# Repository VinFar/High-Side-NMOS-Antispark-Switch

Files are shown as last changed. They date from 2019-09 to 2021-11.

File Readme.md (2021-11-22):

High Side milliOhm NMOS Anti Spark Switch
===
# Introduction

This PCB is an Anti-Spark switch for high capacitive loads (100A, 60V) and was especially designed for electric longboards.
It uses 10 TPW1R306PL milliOhm N-MOSFET, which have a Rdson of around 90 uOhm in the worst case,
which theoretically enables a maximum current of around 125A with sufficient cooling.

Inspired by the [DieBieMS](https://github.com/DieBieEngineering/DieBieMS) it uses a BQ76200PWR HighSide MOSFET driver,
to enable the high switching with NMOS.

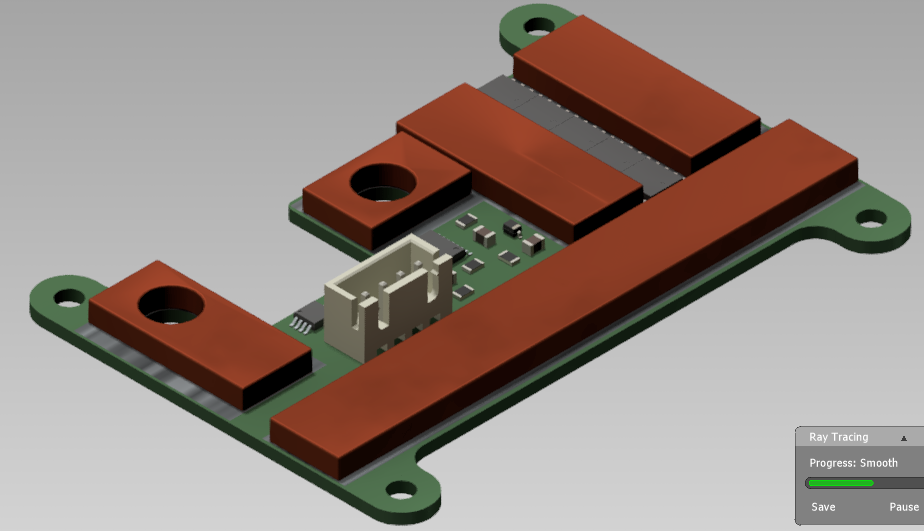
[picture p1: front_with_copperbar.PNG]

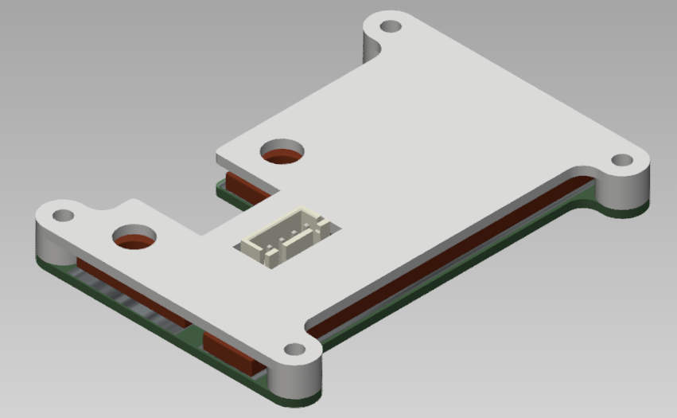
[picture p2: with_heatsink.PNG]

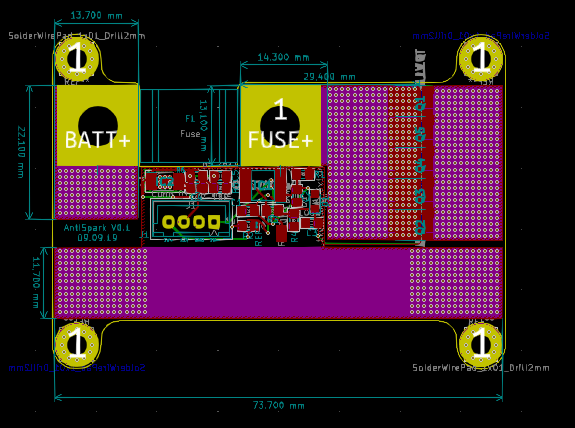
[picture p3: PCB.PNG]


## Features

The PCB includes the following features:
  - dimensions: 74mm x 38.2mm
  - maximum current of at least 125A (more with additional copper and cooling)
  - maximum voltage of 60V
  - controlled dI/dt with capacitor and current limiting resistor
  - 10 TPW1R306PL N-channel MOSFET
  - BQ76200PWR High Side MOSFET Driver
  - A TPS7A4101DGNR 12V 50mA LDO
  - A holder for a LittleFuse BF1
  - 4 pin JST XH connector for external switch or MCU
  - exposed pcb traces to add solder or a copper bar for lower resistance

### Versions
  - V0.1 is the initial version (08.09.19)
  - V0.2 uses 10 TPW1R306PL mosfet instead of two IRFS7530 (09.09.19)

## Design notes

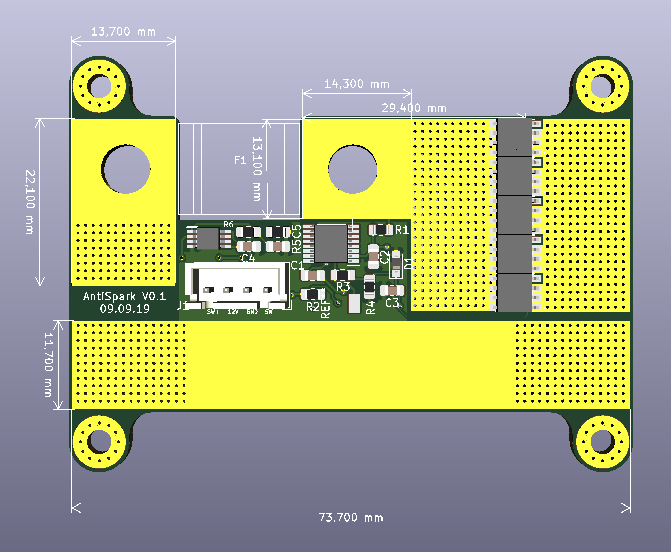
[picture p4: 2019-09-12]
front.PNG

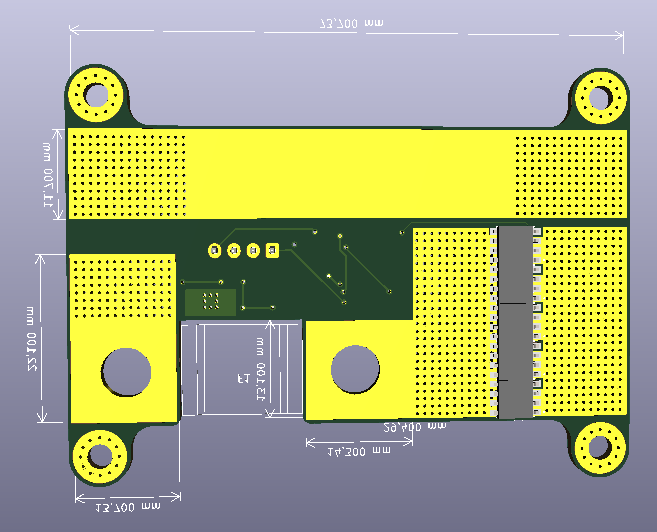
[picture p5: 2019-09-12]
back.PNG

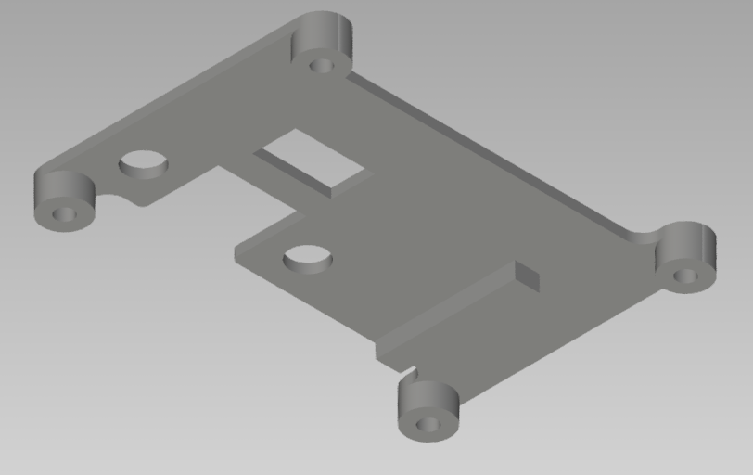
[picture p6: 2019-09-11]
heatsink.PNG

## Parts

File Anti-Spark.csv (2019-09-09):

Reference | Quantity | Value | Footprint | Datasheet | Description | Height | Manufacturer_Name | Manufacturer_Part_Number | Mouser Part Number | Mouser Price/Stock
C1 C4 C5 | 3 | 1uF | Capacitor_SMD:C_0805_2012Metric_Pad1.15x1.40mm_HandSolder | ~
C2 C3 | 2 | 100nF | Capacitor_SMD:C_0805_2012Metric_Pad1.15x1.40mm_HandSolder | ~
D1 | 1 | 18V | Diode_SMD:D_SOD-323_HandSoldering | ~
F1 | 1 | Fuse | SamacSys_Parts:littleFuseBF1 | ~
IC1 | 1 | BQ76200PWR | SOP65P640X120-16N | http://www.ti.com/lit/gpn/bq76200 | High-Side N-Channel FET Driver | 1.2 | Texas Instruments | BQ76200PWR | 595-BQ76200PWR | https://www.mouser.com/Search/Refine.aspx?Keyword=595-BQ76200PWR
IC2 | 1 | TPS7A4101DGNR | SOP65P490X110-9N | http://www.ti.com/lit/gpn/tps7a4101 | 50V Input, 50mA, Single Output Low-Dropout Linear Regulator | 1.1 | Texas Instruments | TPS7A4101DGNR | 595-TPS7A4101DGNR | https://www.mouser.com/Search/Refine.aspx?Keyword=595-TPS7A4101DGNR
J1 | 1 | Conn_01x04_Male | Connector_JST:JST_XH_B4B-XH-A_1x04_P2.50mm_Vertical | ~
Q1 Q2 | 2 | IRFS7530TRL7PP | SamacSys_Parts:IRFS7530 | https://componentsearchengine.com/Datasheets/1/IRFS7530TRL7PP.pdf | MOSFET 60V 240A StrongIRFET D2PAK-7 Infineon IRFS7530TRL7PP N-channel MOSFET Transistor, 240 A, 60 V, 7-Pin D2PAK |  | Infineon | IRFS7530TRL7PP | 942-IRFS7530TRL7PP | https://www.mouser.com/Search/Refine.aspx?Keyword=942-IRFS7530TRL7PP
R1 | 1 | 100 | Resistor_SMD:R_0805_2012Metric_Pad1.15x1.40mm_HandSolder | ~
R2 | 1 | 0 | Resistor_SMD:R_0805_2012Metric_Pad1.15x1.40mm_HandSolder | ~
R3 | 1 | 2M | Resistor_SMD:R_0805_2012Metric_Pad1.15x1.40mm_HandSolder | ~
R4 | 1 | 10M | Resistor_SMD:R_0805_2012Metric_Pad1.15x1.40mm_HandSolder | ~
R5 | 1 | 92.301k | Resistor_SMD:R_0805_2012Metric_Pad1.15x1.40mm_HandSolder | ~
R6 | 1 | 10k | Resistor_SMD:R_0805_2012Metric_Pad1.15x1.40mm_HandSolder | ~

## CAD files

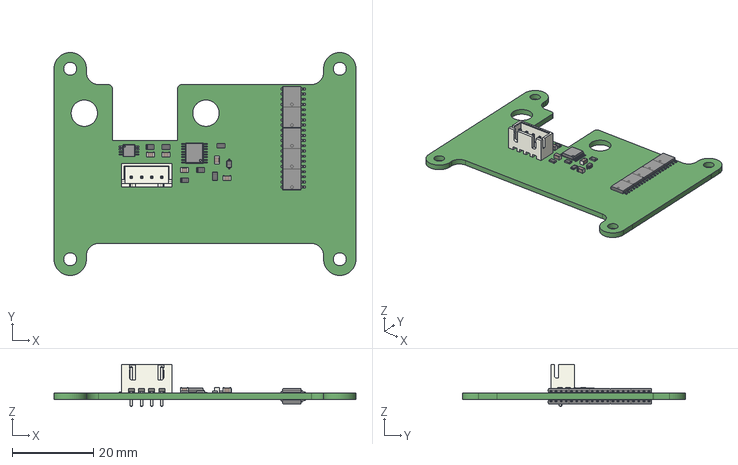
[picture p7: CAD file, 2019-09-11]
Anti-Spark.step
74.5 x 55.0 x 10.4 mm

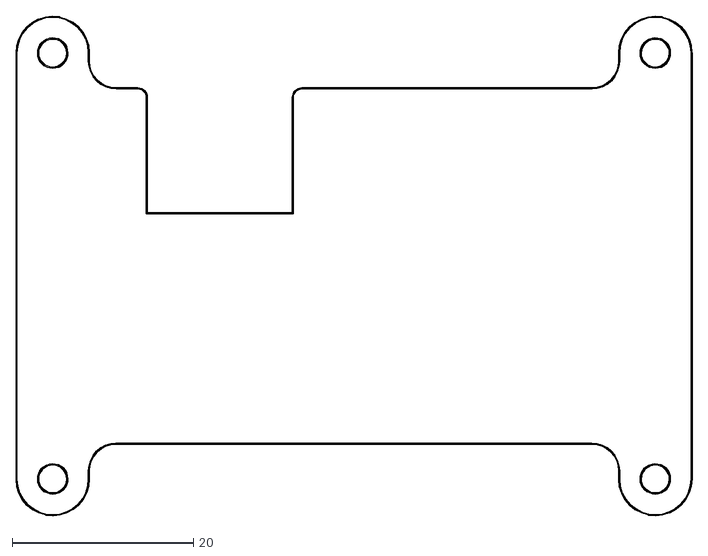
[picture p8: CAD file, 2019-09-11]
Gerber/DXF/Anti-Spark-Edge_Cuts.dxf
74.6 x 55.1

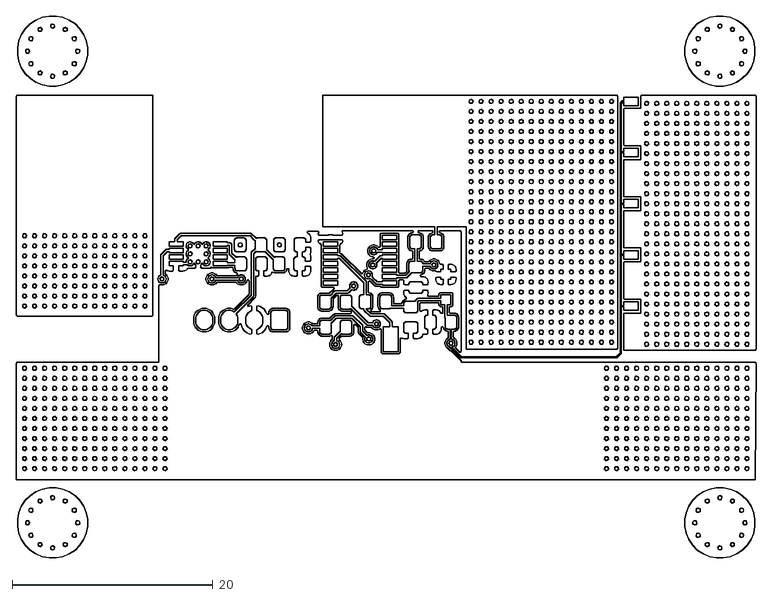
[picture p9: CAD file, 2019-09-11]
Gerber/DXF/Anti-Spark-F_Cu.dxf
73.7 x 54.0

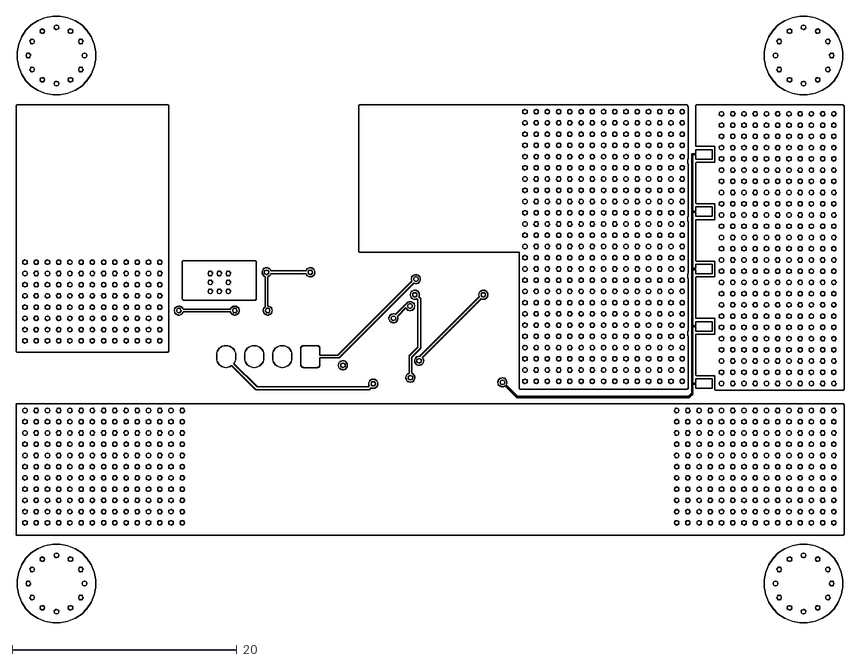
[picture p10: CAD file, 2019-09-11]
Gerber/DXF/Anti-Spark-B_Cu.dxf
73.7 x 54.0

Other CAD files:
Anti-Spark.iam
BQ76200PWR.iam
COMPOUND.ipt
COMPOUND_1.ipt
COMPOUND_2.ipt
C_0805_2012Metric.iam
D_SOD-323.iam
Gerber/DXF/Anti-Spark-B_Mask.dxf
Gerber/DXF/Anti-Spark-B_SilkS.dxf
Gerber/DXF/Anti-Spark-F_Mask.dxf
Gerber/DXF/Anti-Spark-F_SilkS.dxf
JST_XH_B4B-XH-A_1x04_P2.50mm_Vertical.iam
R_0805_2012Metric.iam
SOLID.ipt
SOLID_1.ipt
SOLID_2.ipt
SOLID_3.ipt
SOLID_4.ipt
SOT1215.iam
TPS7A4101DGNR.iam
heatsink.iam

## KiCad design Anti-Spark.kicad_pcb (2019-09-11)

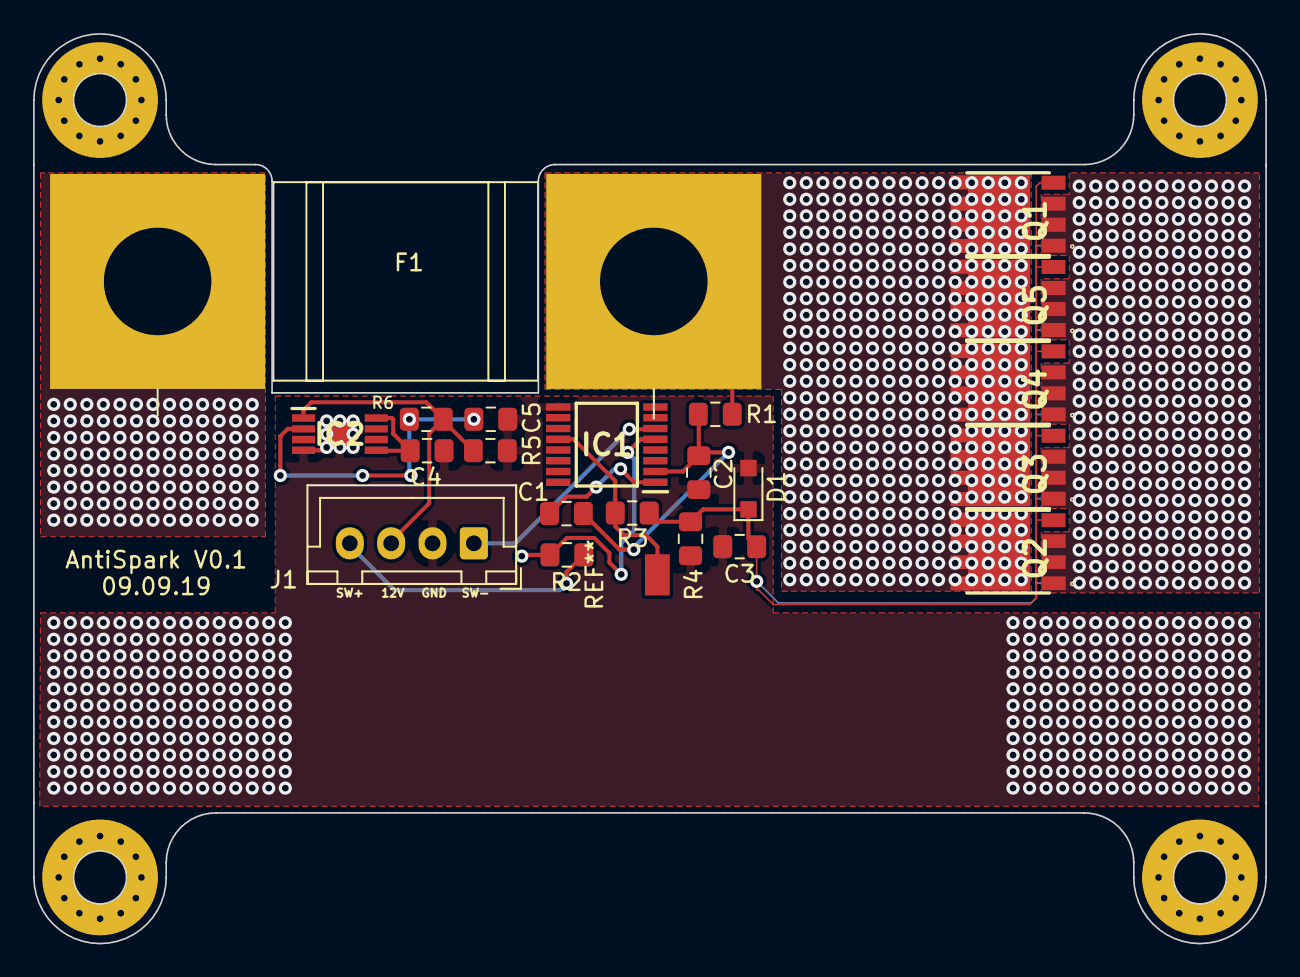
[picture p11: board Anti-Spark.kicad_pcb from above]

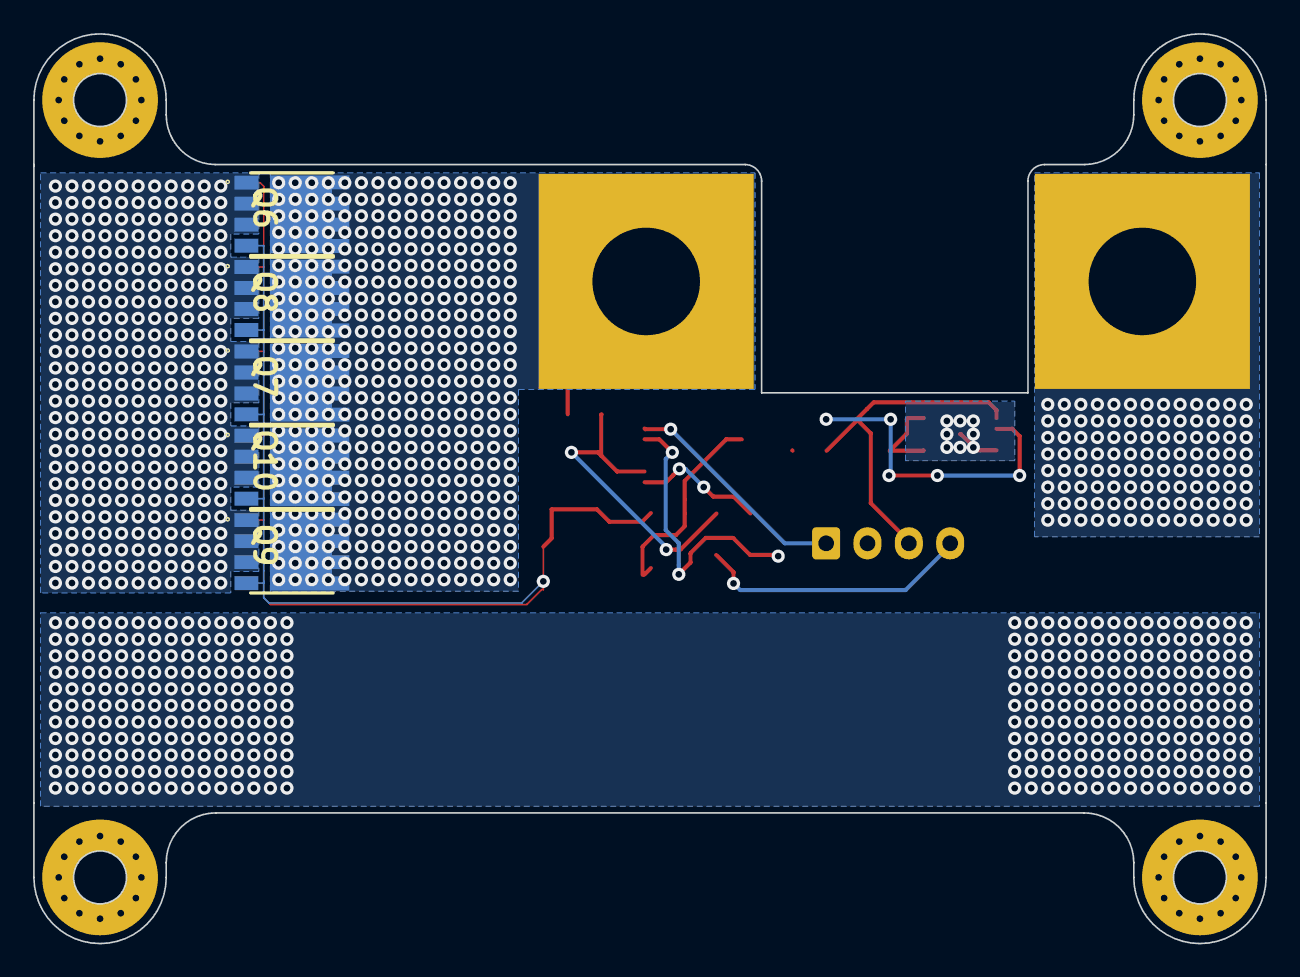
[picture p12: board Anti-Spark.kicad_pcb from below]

Board: 2 copper layers, 74.5 x 55.0 mm, 26 parts (5 on the bottom side), 13 nets.

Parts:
C1, C4, C5: 1uF; C_0805_2012Metric_Pad1.15x1.40mm_HandSolder
C2, C3: 100nF; C_0805_2012Metric_Pad1.15x1.40mm_HandSolder
D1: 18V; D_SOD-323_HandSoldering
F1: Fuse; littleFuseBF1
IC1: BQ76200PWR; SOP65P640X120-16N
IC2: TPS7A4101DGNR; SOP65P490X110-9N
J1: Conn_01x04_Male; JST_XH_B4B-XH-A_1x04_P2.50mm_Vertical
Q1, Q2, Q3, Q4, Q5, Q6, Q7, Q8, Q9, Q10: TPW1R306PL,L1Q; SOP_ADVANCE
R1: 100; R_0805_2012Metric_Pad1.15x1.40mm_HandSolder
R2: 0; R_0805_2012Metric_Pad1.15x1.40mm_HandSolder
R3: 2M; R_0805_2012Metric_Pad1.15x1.40mm_HandSolder
R4: 10M; R_0805_2012Metric_Pad1.15x1.40mm_HandSolder
R5: 92.301k; R_0805_2012Metric_Pad1.15x1.40mm_HandSolder
R6: 10k; R_0805_2012Metric_Pad1.15x1.40mm_HandSolder

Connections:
-BATT: C2.2, C3.2, C4.2, C5.2, D1.2, IC1.9, IC2.4, IC2.9, J1.2, R4.2, R5.1
FUSE+: F1.1, Q1.5, Q1.6, Q1.7, Q1.8, Q1.9, Q2.5, Q2.6, Q2.7, Q2.8, Q2.9, Q3.5, Q3.6, Q3.7, Q3.8, Q3.9, Q4.5, Q4.6, Q4.7, Q4.8, Q4.9, Q5.5, Q5.6, Q5.7, Q5.8, Q5.9, Q6.5, Q6.6, Q6.7, Q6.8, Q6.9, Q7.5, Q7.6, Q7.7, Q7.8, Q7.9, Q8.5, Q8.6, Q8.7, Q8.8, Q8.9, Q9.5, Q9.6, Q9.7, Q9.8, Q9.9, Q10.5, Q10.6, Q10.7, Q10.8, Q10.9, R1.1
unnamed: C1.1, IC1.1
unnamed: C1.2, C2.1, IC1.2, R1.2
unnamed: C3.1, D1.1, Q1.4, Q2.4, Q3.4, Q4.4, Q5.4, Q6.4, Q7.4, Q8.4, Q9.4, Q10.4, R3.2, R4.1
unnamed: C4.1, IC2.5, IC2.8
unnamed: C5.1, IC2.1, J1.3, R6.2
unnamed: IC1.5, R2.2
unnamed: IC1.12, R3.1
unnamed: IC2.2, R5.2, R6.1
SW+: J1.4, R2.1
SW-: IC1.6, J1.1
VESC: Q1.1, Q1.2, Q1.3, Q2.1, Q2.2, Q2.3, Q3.1, Q3.2, Q3.3, Q4.1, Q4.2, Q4.3, Q5.1, Q5.2, Q5.3, Q6.1, Q6.2, Q6.3, Q7.1, Q7.2, Q7.3, Q8.1, Q8.2, Q8.3, Q9.1, Q9.2, Q9.3, Q10.1, Q10.2, Q10.3

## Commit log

2019-09-08 add: gnd plane for logic
    [Anti-Spark.kicad_pcb]
2019-09-08 add: autosave from KiCad
2019-09-08 ch: image of pcb
2019-09-08 ch: max current
2019-09-08 ch: features, current
2019-09-09 ch: new version with 10 mosfets
    [Anti-Spark.csv, Anti-Spark.kicad_pcb, Anti-Spark.sch]
2019-09-11 updated PCB to V0.1
    [Anti-Spark-B_Cu.gbl, Anti-Spark-B_Mask.gbs, Anti-Spark-B_SilkS.gbo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]
2019-09-11 add: step of pcb, copper and heatsink
    [Anti-Spark-B_Cu.dxf, Anti-Spark-B_Mask.dxf, Anti-Spark-B_SilkS.dxf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]
2019-09-12 ch: pictures
    [heatsink.iam]
2021-11-22 updated schematic to V0.2 Board file is corrupted
    [Anti-Spark.sch]
